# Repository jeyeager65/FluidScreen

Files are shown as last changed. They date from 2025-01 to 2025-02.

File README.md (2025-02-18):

# FluidScreen
Wireless controller for FluidNC

e19302e4588211ce1077c6e39101f643c2d2b93d


## Overview
This is a wireless controller (except for power) for a 3 axis CNC machine running FluidNC.  It connects to FluidNC via a WebSocket connection.  This uses an ESP32 and is written in C++ using PlatformIO.

# Features
- General - Hold, Resume, Unlock, Reset
- Jogging - In XY, X, Y, or Z using the physical joystick.  The further the joystick is from the center, the faster the feedrate.  The value does have a curve to make it easier to perform slow jogging with small movements.
- Home - All, X, Y, or Z
- Macro - Special macro format using GCode parameters and expression functionality of FluidNC.  Supports up to 6 custom defined macros with a description of each displayed on the screen.
- Configuration - Display a captive portal webpage for updating configuration.
  - Wifi/FluidNC - Set Wifi and FluidNC settings.
  - Theming - This is a bit extra but the individual theme and status colors can be updated.
- Hold Messages - Displays the last message on the screen.  When a hold occurs, the last message is displayed with the Resume option activated.

# Parts

## Hardware
> The 3D printed case was made for these specific components. If alternates are used, I am not certain if things will fit properly.
- 1x ESP32 Devkit - https://www.amazon.com/Espressif-ESP32-DevKitC-32E-Development-Board/dp/B09MQJWQN2
- 1x Joystick - https://www.amazon.com/gp/product/B0CPFDKWZF
- 1x Rotary Encoder - https://www.amazon.com/gp/product/B06XQTHDRR
- 1x Display - https://www.amazon.com/gp/product/B073R7BH1B
- 1x 10uF Capacitor - This allows for flashing the firmware without needing to press the Boot button on the ESP32. Otherwise, the ESP32 would need to be removed to access the Boot button.

## Miscellaneous
- ~16x M3x6mm Screws
- Female to Female Dupont Wires
- Dupont Connector Kit - This is optional. It is helpful to have a 9 or 10 plug connector for combining all the wires for the screen into a single plug. https://www.amazon.com/gp/product/B08X6C7PZM
- USB Micro Cable - For power and flashing firmware.  Ensure it is a data and power cable, not just power only.
- Solder Seal Heat Shrink Butt Connectors - This is optional and was used for joining wires to share 3.3v and ground. Used the red 18-22 awg from this kit: https://www.amazon.com/dp/B083LZS69N
  - Heat Gun - https://www.amazon.com/dp/B08VFY8THD

## 3D Print
> These were printed in PLA with 3 walls and 50% infill with a 0.4mm nozzle at 0.2mm layer height.
- 1x Case Top - Print with flat part on build plate. No supports necessary.
- 1x Case Bottom - Print with flat part on build plate. Supports required for screw holes on bottom.
- 1x ESP32 Holder - Print with flat part on build plate.  Supports required for screw holes on bottom.
- 1x Encoder Knob - Print with flat part on build plate.  Supports may be required for indent.
- 4x Washer - This is optional. A few M3 washers can be used instead. This is necessary for attaching the screen to the case top because otherwise the M3x6mm screws are too long.  Alternatively, M3x4mm screws could be used.

# Firmware

## Pre-Requisites
1. Visual Studio Code (https://code.visualstudio.com/) with "PlatformIO IDE" extension installed.
2. Silicon Labs CP210x USB to UART Bridge Driver (https://www.silabs.com/developer-tools/usb-to-uart-bridge-vcp-drivers?tab=downloads)
3. Download or checkout this repository.

## Installation
> Note: If this project has not been assembled yet or the ESP32 is standalone, the "Boot" button on the ESP32 will need to be held for a couple seconds when it starts to upload the filesystem image and when it flashes the firmware.

1. Open the Source folder in Visual Studio Code.
2. Connect the ESP32 to the computer with a USB cable.
3. Click the PlatformIO icon on the left.
4. Under "Project Tasks", select "esp32dev" -> "Platform", select the "Build Filesystem Image" task to create the filesystem image.
5. Under "Platform", select the "Upload Filesystem Image" task to upload.
6. Under "Project Tasks", select "esp32dev" -> "General", select the "Build" task to build the project.
7. Under "General", select the "Upload" task to upload the firmware.

# Assembly







## Pin Mappings

### Display
> Note: Touch Pins are not used.

| Pin | ESP32 Pin |
| --- | --- |
| VCC | 3V3 |
| GND | GND |
| CS | 5 |
| RESET | 17 |
| DC | 16 |
| SDI(MOSI) | 23 |
| SCK | 18 |
| LED | 22 |
| SDI(MISO) | 19 |

### Joystick
> Note: SW pin is not used.

| Pin | ESP32 Pin |
| --- | --- |
| GND | GND |
| +5V | 3V3 |
| VRX | 32 |
| VRY | 33 |

### Rotary Encoder
| Pin | ESP32 Pin |
| --- | --- |
| GND | GND |
| + | 3V3 |
| SW  | 27 |
| DT  | 25 |
| CLK | 26 |

### Capacitor
| Pin | ESP32 Pin |
| --- | --- |
| Short Leg with White | GND |
| Long Leg | EN |

## Steps
> With the pin mappings and pictures, it can likely be assembled without these instructions.

### Bottom
1. Start with the case bottom (thinner part with USB hole at the bottom).
2. Attach the joystick and rotary encoder with M3x6mm screws with male pins pointed at the bottom.
3. Place the ESP32 upside down with the antenna at the top. It should rest on the standoffs.
4. Attach the ESP32 holder with M3x6mm screws with the flat part up.  It should bend to apply some pressure to the ESP32 to hold it in place.
5. Create wire for sharing 3.3v connection with 4 ends, 2 on each side.  Verify lengths are appropriate and ensure there is extra length for removal of the top.  This can be done with solder seal heat shrink butt connectors, lever nuts, or just solder and heat shrink.
6. Run the wire under the bottom part of the ESP32 close to the USB end.
7. Connect the 3.3V wires to the appropriate pins on the ESP32, joystick, rotary encoder, and display.
8. Create wire for sharing GND connection with 3 ends.  This is for connecting the joystick and display. (The ESP32 has 3 GND connections. The capacitor and rotary encoder can use their own pins.)
9. Connect the GND wires to the appropriate pins on the ESP32 and joystick.
10. Connect a separate ground wire between the ESP32 and rotary encoder.
11. Connect the remaining wires for the joystick and rotary encoder as described in the pin mapping section.
12. Crimp connectors to the 10uF capacitor and attach to the ESP32 between the EN and GND pins towards the top of the connector. Ensure the short leg with the white line attaches to the GND pin.

### Top
1. Place the screen into the case top with the pins on the joystick side. The screen should be about 1mm below the surface.
2. Attach the screen with M3x6mm screws and printed washers (or 4mm screws or ~3 M3 washers).
3. Connect the wires for the display.  It is recommended to use a 9 or 10 pin dupont connector to create a single connection to the display.  This can be done making your own cables or by removing the single plastic housing and plugging it into the new larger connector.

### Finish
1. Attach the case bottom to the case top with 4 M3x6mm screws. These screws can be longer.
2. Press the printed knob onto the rotary encoder.

# Macros
The macro menu allows for up to 6 custom defined macros.  These are defined in a file that must be named "_screenmacros.gcode" and placed in the root on the SD card.

## Template
``` gcode
o100 if[#<_screenMacro> EQ 1]
  o101 if[#<_screenMacroInfoOnly> EQ 1]
    (MSG, Macro 1 - Description)
  o101 else
    (MSG, Running Macro 1)
  o101 end if
o100 elseif[#<_screenMacro> EQ 2]
  o102 if[#<_screenMacroInfoOnly> EQ 1]
    (MSG, Macro 2 - Description)
  o102 else
    (MSG, Running Macro 2)
  o102 end if
o100 elseif[#<_screenMacro> EQ 2]
  o103 if[#<_screenMacroInfoOnly> EQ 1]
    (MSG, Macro 3 - Description)
  o103 else
    (MSG, Running Macro 3)
  o103 end if
o100 elseif[#<_screenMacro> EQ 4]
  o104 if[#<_screenMacroInfoOnly> EQ 1]
    (MSG, Macro 4 - Description)
  o104 else
    (MSG, Running Macro 4)
  o104 end if
o100 elseif[#<_screenMacro> EQ 5]
  o105 if[#<_screenMacroInfoOnly> EQ 1]
    (MSG, Macro 5 - Description)
  o105 else
    (MSG, Running Macro 5)
  o105 end if
o100 elseif[#<_screenMacro> EQ 6]
  o106 if[#<_screenMacroInfoOnly> EQ 1]
    (MSG, Macro 6 - Description)
  o106 else
    (MSG, Running Macro 6)
  o106 end if
o100 else
  (PRINT, Macro %d#<_screenMacro>: Not Defined)
o100 end if
```

## How It Works
This utilizes the GCode Parameters and Expressions functionality in FluidNC: http://wiki.fluidnc.com/en/features/gcode_parameters_expressions

When highlighting a macro number on the screen, the following code is run to set the variables where "N" is the highlighted macro number:
``` gcode
#<_screenMacroInfoOnly>=1
#<_screenMacro>=N
$SD/Run=_screenmacros.gcode
```

## Example
``` gcode
o100 if[#<_screenMacro> EQ 1]
  o101 if[#<_screenMacroInfoOnly> EQ 1]
    (MSG, Run Current GCode - Run the GCode file defined in /ScreenMacros/current.gcode.)
  o101 else
    (MSG, Running Current GCode Macro)
    $SD/Run=/ScreenMacros/current.gcode
  o101 end if
o100 elseif[#<_screenMacro> EQ 2]
  o102 if[#<_screenMacroInfoOnly> EQ 1]
    (MSG, View Pulloffs - View the current X, Y, and Z pulloffs.)
  o102 else
    (MSG, Running View Pulloffs Macro)
    M0 (PRINT, Motor Pulloffs: X=%.3f#</axes/x/motor0/pulloff_mm>  Y0=%.3f#</axes/y/motor0/pulloff_mm>  Y1=%.3f#</axes/y/motor1/pulloff_mm>  Z0=%.3f#</axes/z/motor0/pulloff_mm>  Z1=%.3f#</axes/z/motor1/pulloff_mm>)
  o102 end if
o100 elseif[#<_screenMacro> EQ 3]
  o103 if[#<_screenMacroInfoOnly> EQ 1]
    (MSG, Z Level - Z level the gantry by probing Z on both sides and setting set Z pulloffs.)
  o103 else
    (MSG, Running Z Level Macro)
    $SD/Run=_zlevel.gcode
  o103 end if
o100 else
  (PRINT, Macro %d#<_screenMacro>: Not Defined)
o100 end if
```

When clicking on the highlighted macro, the same code is run except the _screenMacroInfoOnly variable is set to 0 (false).

This allows the script to know which macro and whether or not it should just display a description message or actually run the macro.

# Notes

## Future Enhancements
> None of these are guaranteed but are things I would like to do in the future.
- Add battery with charging circuit
- Add a dock (or even a magnetic charging dock)
- Make the case thinner possibly by using a mini ESP32 instead of a devkit

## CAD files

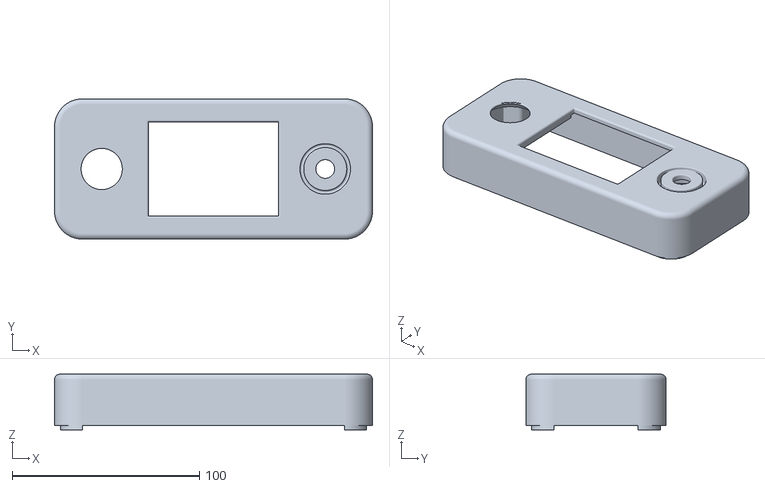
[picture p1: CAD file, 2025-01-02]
3dPrint/Case Top.stl
170.0 x 75.0 x 29.8

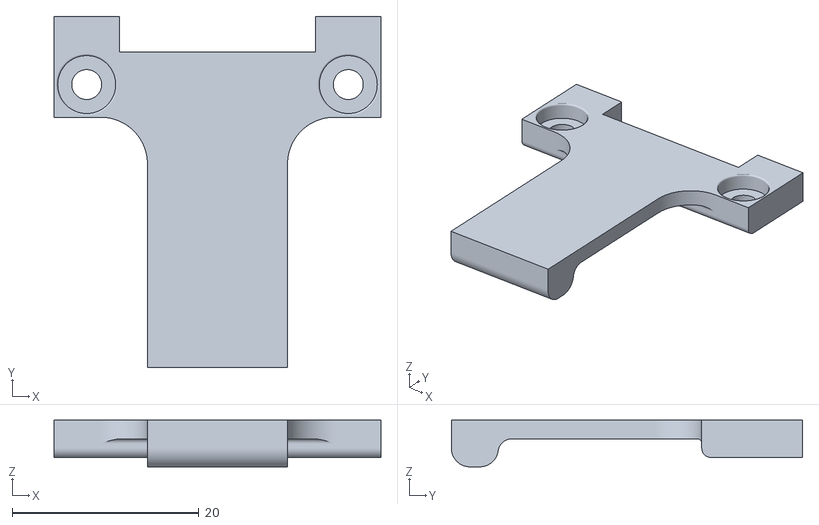
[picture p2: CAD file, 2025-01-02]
3dPrint/ESP32 Holder.stl
35.0 x 37.6 x 5.00

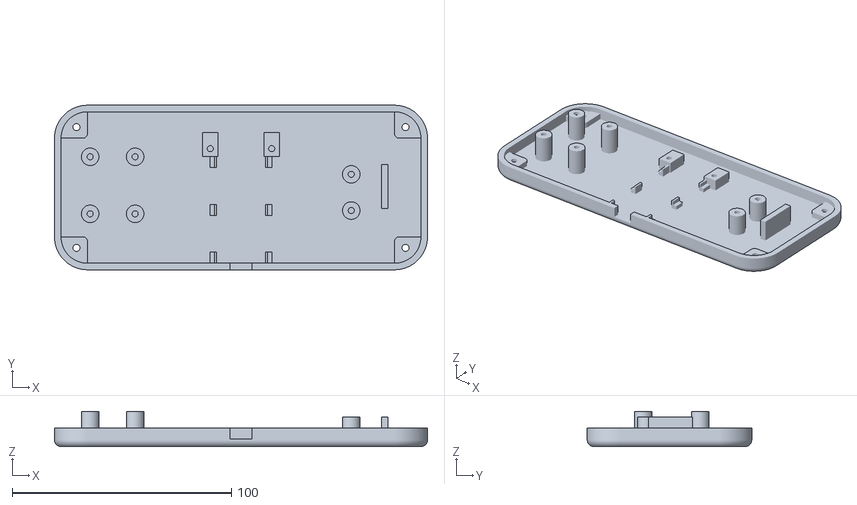
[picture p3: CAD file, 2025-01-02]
3dPrint/Case Bottom.stl
170.0 x 75.0 x 16.0

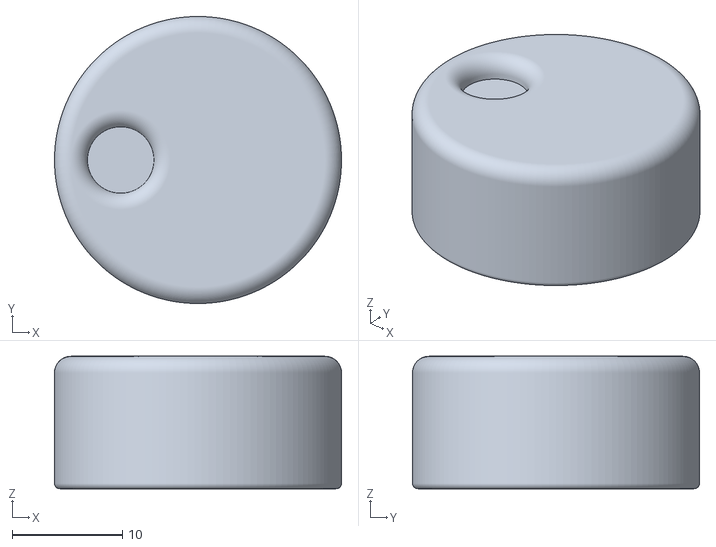
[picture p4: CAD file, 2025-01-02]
3dPrint/Knob.stl
26.0 x 26.0 x 12.0

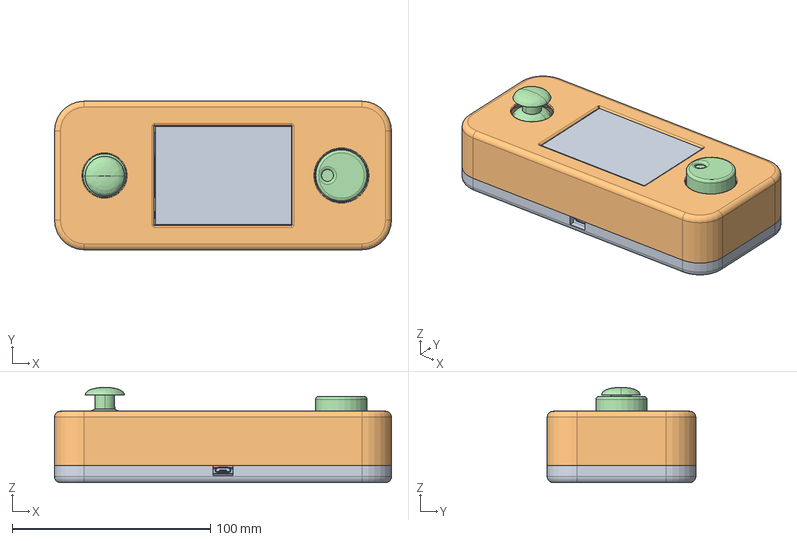
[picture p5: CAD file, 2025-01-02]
3dPrint/FluidScreen.FCStd
170.0 x 75.0 x 48.0 mm
Case Bottom
Case Top
ESP32 Holder
Knob
plate and holes
circle001
circle002
circle003
circle004
border001
border002
ShapeString099
ShapeString100
ShapeString102
ShapeString103
cupper_upper
cupper_bottom
mask_bottom
res_silk
res_silk001
res_silk002
res_silk003
res_silk004
res_silk005
cap_silk_up
cap_silk_dwn
cap_silk_up001
cap_silk_dwn001
sot23_left
sot23_right
sot23_left001
sot23_right001
u2_silk002
sd_silk001
line_silk001
line_silk002
ShapeString067
ShapeString105
ShapeString106
ShapeString107
ShapeString108
ShapeString068
ShapeString110
ShapeString111
ShapeString112
ShapeString113
ShapeString069
ShapeString115
ShapeString116
ShapeString117
ShapeString070
ShapeString119
ShapeString120
ShapeString121
ShapeString122
ShapeString071
ShapeString124
ShapeString125
ShapeString126
ShapeString073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

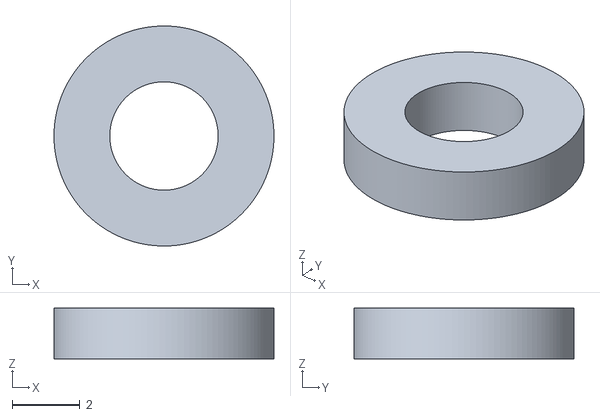
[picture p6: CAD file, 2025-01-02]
3dPrint/Washer.stl
6.50 x 6.50 x 1.50

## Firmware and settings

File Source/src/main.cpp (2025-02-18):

#include <Adafruit_GFX.h>
#include <Adafruit_ILI9341.h>
#include <Fonts/FreeSans9pt7b.h>
#include <Fonts/FreeSansBold12pt7b.h>
#include <Fonts/FreeSans12pt7b.h>
#include <Fonts/FreeMono9pt7b.h>
#include <Arduino.h>
#include <math.h>
#include <WiFi.h>
#include <WebSocketsClient.h>
#include "JogJoystick.h"
#include <ESPRotary.h>
#include "menu.h"
#include "qrcode.h"
#include "FluidScreenSettings.h"

void setupColors(FluidScreenSettings& settings);
void drawConfig();
void drawPreview();
void drawMessage();
void drawMessage(String message);
void initWebSocket();

#include "CaptivePortal.h"
#include "SPIFFS.h"

const char* version = "1.0.1-20250218";

bool wsFirstConnectAttempt = true;
bool wsDisconnected = false;

// Rotary Encoder Settings
volatile int encoderCounter = 0;
int encoderPrevCounter;
volatile int encoderMaxCount = 20;
int buttonState;
unsigned long lastButtonTime = 0;

const byte ENCODER_CLK_PIN = 25;
const byte ENCODER_DT_PIN = 26;
const byte ENCODER_SW_PIN = 27;

const int tftWidth = 320;
const int tftHeight = 240;

// Info Screen
String messageCurrent;
String messagePrevious;


ESPRotary menuEncoder;
hw_timer_t *timer = NULL;

void IRAM_ATTR handleLoop() {
  menuEncoder.loop();
}

// Joystick Canvas
GFXcanvas16 joystickCanvas(120, 120);
GFXcanvas16 jsInfoCanvas(100, 100);

// Joystick Pins
const int JOYSTICK_X_PIN = 33;
const int JOYSTICK_Y_PIN = 32;

// Display TFT Pins
const int TFT_CS_PIN = 5;
const int TFT_DC_PIN = 16;
const int TFT_RST_PIN = 17;
const int TFT_BL_PIN = 22;

unsigned long lastDrawTime = 0;
unsigned long drawDelay = 50;

unsigned long lastMacroInfoTime = 0;
unsigned long macroInfoDelay = 300;

uint16_t feedrate = 0;
unsigned long lastJogTime = 0;
unsigned long jogDelay = 200;
bool jogActive = false;

// Colors
// RGB565 Colors - https://learn.adafruit.com/adafruit-gfx-graphics-library/coordinate-system-and-units
// Converter - https://barth-dev.de/online/rgb565-color-picker/
uint16_t COLOR_PRIMARY           = 0x01EC;  // #003d63
uint16_t COLOR_SECONDARY         = 0x434F;  // #42697b
uint16_t COLOR_BG                = 0x0841;  // #080808
uint16_t COLOR_BG_ALT            = 0x39C7;  // #3a393a
uint16_t COLOR_BG_PANEL          = 0x2104;  // #212021
uint16_t COLOR_BORDER            = 0xBE19;  // #bdc2ce
uint16_t COLOR_SELECT            = 0x0397;  // #0071bd
uint16_t COLOR_TEXT              = 0xFFFF;  // #ffffff
uint16_t COLOR_QR                = 0x0000;  // #000000
uint16_t COLOR_QR_BG             = 0xFFFF;  // #ffffff

uint16_t COLOR_STATUS_DEFAULT    = 0x7BEF;  // #7b7d7b
uint16_t COLOR_STATUS_IDLE       = 0x7BEF;  // #7b7d7b
uint16_t COLOR_STATUS_JOG        = 0x000F;  // #00007b
uint16_t COLOR_STATUS_RUN        = 0x03E0;  // #007d00
uint16_t COLOR_STATUS_HOLD       = 0xE660;  // #e6ce00
uint16_t COLOR_STATUS_HOME       = 0x03EF;  // #007d7b
uint16_t COLOR_STATUS_ALARM      = 0xF800;  // #ff0000
uint16_t COLOR_STATUS_DISCONNECT = 0x780F;  // #7b007b
uint16_t COLOR_STATUS_CONFIG     = 0xFB80;  // #ff7100

uint16_t JOG_MAX_FEEDRATE_XY     = 2400;
uint16_t JOG_MAX_FEEDRATE_Z      = 800;

// Display Values
String grblState = "UNKNOWN";
String grblStatePrev = "UNKNOWN";
String mPosX = " ", mPosY = " ", mPosZ = " ";
String mPosXPrev = "*", mPosYPrev = "*", mPosZPrev = "*";
String lastMessage;

JogJoystick joystick(JOYSTICK_X_PIN, JOYSTICK_Y_PIN);

Adafruit_ILI9341 tft = Adafruit_ILI9341(TFT_CS_PIN, TFT_DC_PIN, TFT_RST_PIN);

WebSocketsClient webSocket;

bool initWiFi() 
{
  if(WiFi.status() == WL_CONNECTED) {
    return true;
  }

  int retryCount = 20;
  WiFi.mode(WIFI_STA);
  WiFi.setAutoReconnect(true);
  WiFi.begin(CurrentSettings.Connection.SSID, CurrentSettings.Connection.Password);
  Serial.print("Connecting to WiFi ..");
  while (WiFi.status() != WL_CONNECTED) {
    Serial.print('.');

    if(retryCount > 0) {
      delay(1000);
      retryCount--;
    }
    else {
      WiFi.setAutoReconnect(false);
      return false;
    }
  }
  Serial.println(WiFi.localIP());
  return true;
}

String convert(uint8_t *str, int length)
{
  return String((char *)str, length);
}

void setupTextArea(int x, int y, int width, int height, bool drawBorder = false, int leftMargin = 0, int lineHeight = 30, int negYOffset = 10, uint16_t bgColor = COLOR_BG) {
  tft.setCursor(x+leftMargin, y+lineHeight-negYOffset);
  tft.fillRect(x, y, width, height, bgColor);
  
  if(drawBorder) {
    tft.drawRect(x, y, width, height, COLOR_BORDER);
  }
  
  tft.setTextColor(COLOR_TEXT);
  tft.setFont(&FreeSans9pt7b);
}

void drawSubMenu(const String* subMenu, const int subMenuSize, int subMenuSelected) {
  int menuHeight = 24;

  tft.fillRect(0, 240-(menuHeight*2), 320, menuHeight, COLOR_SECONDARY);
  tft.drawRect(0, 240-(menuHeight*2), 320, menuHeight, COLOR_BORDER);

  int itemSize = 320/subMenuSize;
  int rightX = 0;
  for(int j = 0; j < subMenuSize; j++) {
    tft.setCursor(j*itemSize, 234-menuHeight);
    tft.setFont(&FreeSans9pt7b);
    if(j == subMenuSelected) {
      tft.fillRect((j*itemSize)+1,240-(menuHeight*2)+1,itemSize-1,menuHeight-2,COLOR_SELECT);
    }
    tft.setTextColor(COLOR_TEXT);

    int16_t x1, y1, xCenterStart;
    uint16_t width, height;
    tft.getTextBounds(subMenu[j], j*itemSize, 234-menuHeight, &x1, &y1, &width, &height);
    xCenterStart = x1 + (width/2);

    tft.setCursor((j*itemSize) + ((itemSize-width)/2), 234-menuHeight);
    tft.print(subMenu[j]);
    tft.drawLine((j+1)*itemSize, 240-(menuHeight*2), (j+1)*itemSize, 240-menuHeight, COLOR_BORDER);
  }
}

void drawMenu() {
  int menuHeight = 24;

  tft.fillRect(0, 240-menuHeight, 320, menuHeight, COLOR_PRIMARY);
  tft.drawRect(0, 240-menuHeight, 320, menuHeight, COLOR_BORDER);

  int itemSize = 320/menuSize;
  
  for(int i = 0; i < menuSize; i++) {
    tft.setCursor(i*itemSize, 234);
    tft.setFont(&FreeSans9pt7b);
    if(i == menuSelected) {
      tft.fillRect((i*itemSize)+1,240-menuHeight+1,itemSize-1,menuHeight-2,COLOR_SELECT);
    }
    tft.setTextColor(COLOR_TEXT);

    // Center Text
    int16_t x1, y1, xCenterStart;
    uint16_t width, height;
    tft.getTextBounds(menu[i], i*itemSize, 234, &x1, &y1, &width, &height);
    xCenterStart = x1 + (width/2);

    tft.setCursor(x1 + ((itemSize-width)/2), 234);
    tft.print(menu[i]);
    tft.drawLine((i+1)*itemSize, 240-menuHeight, (i+1)*itemSize, 240, COLOR_BORDER);
  }

  // Draw submenu
  tft.fillRect(0, 240-(menuHeight*2), 320, menuHeight, COLOR_PRIMARY);
  tft.drawRect(0, 240-(menuHeight*2), 320, menuHeight, COLOR_BORDER);

  if(menu[menuSelected] == "Jog") {
    drawSubMenu(jogMenu, jogMenuSize, jogMenuSelected);
  }
  else if(menu[menuSelected] == "Home") {
    drawSubMenu(homeMenu, homeMenuSize, homeMenuSelected);
  }
  else if(menu[menuSelected] == "Macro") {
    drawSubMenu(macroMenu, macroMenuSize, macroMenuSelected);

    // Ensure macro message is displayed
    if(macroMenuSelected == 0) {
      drawMessage(macroMessage);
    }
  }
  else if(menu[menuSelected] == "Other") {
    drawSubMenu(otherMenu, otherMenuSize, otherMenuSelected);
  }
  else if(menu[menuSelected] == "Main") {
    drawSubMenu(controlMenu, controlMenuSize, controlMenuSelected);
  }
}

void drawMessage(String message) {
  int16_t x1, y1;
  uint16_t width, height;

  setupTextArea(0,50,320,135);

  tft.fillRoundRect(0,50+5, 320, 135-5, 5, COLOR_BG_ALT);
  tft.drawRoundRect(0,50+5, 320, 135-5, 5, COLOR_BORDER);

  // Clean Message
  if(message.startsWith("[MSG:")) {
    int startIndex = message.indexOf(":", 5)+2;
    int tempStartIndex = message.indexOf(",", startIndex+1);
    if(tempStartIndex >= 0) { startIndex = tempStartIndex+2; }
    int endIndex = message.lastIndexOf("]");
    message = message.substring(startIndex, endIndex);
  }

  message.trim();

  // Break at spaces
  bool includeSpace = false;
  char * ptr;
  int length = message.length();
  char buffer[length];
  sprintf(buffer, "%s", message.c_str());

  tft.setFont(&FreeSans9pt7b);
  
  tft.setCursor(5,74);
  tft.setTextWrap(true);

  ptr = strtok(buffer, " ");
  while (ptr != NULL)
  {
    tft.getTextBounds(ptr, tft.getCursorX(), tft.getCursorY(), &x1, &y1, &width, &height);

    if(x1 + width > 320-20) {
      tft.println("");
      tft.setCursor(5, tft.getCursorY());
      includeSpace = false;
    }

    if(includeSpace) {
      tft.print(" ");
    }
    
    tft.printf("%s", ptr);
    ptr = strtok(NULL, " ");
    includeSpace = true;
  }
}

void drawMessage() {
  drawMessage(lastMessage); 
}

void drawStatus(String status, bool preventDuplicate = true) {
  bool isHold = status.startsWith("Hold");
  bool isAlarm = status == "Alarm";
  
  grblState = status;
  if(preventDuplicate && grblState == grblStatePrev) return;

  grblStatePrev = grblState;

  tft.setCursor(0, 0+30-7);
  tft.setTextColor(COLOR_TEXT);

  uint16_t statusColor = COLOR_STATUS_DEFAULT;
  if(status == "Idle") statusColor = COLOR_STATUS_IDLE;
  else if(status == "Jog") statusColor = COLOR_STATUS_JOG;
  else if(status == "Run") statusColor = COLOR_STATUS_RUN;
  else if(status.startsWith("Hold")) statusColor = COLOR_STATUS_HOLD;
  else if(status == "Home") statusColor = COLOR_STATUS_HOME;
  else if(status == "Alarm") statusColor = COLOR_STATUS_ALARM;
  else if(status == "Disconnected") statusColor = COLOR_STATUS_DISCONNECT;
  else if(status == "Configuration") statusColor = COLOR_STATUS_CONFIG;

  tft.fillRect(0, 0, 320, 30, statusColor);
  tft.drawRect(0, 0, 320, 30, COLOR_BORDER);

  // Override Font
  tft.setFont(&FreeSansBold12pt7b);
  
  status.toUpperCase();

  int16_t x1, y1, xCenterStart;
  uint16_t width, height;
  tft.getTextBounds(status, 0, 0, &x1, &y1, &width, &height);
  xCenterStart = x1 + (width/2);
  tft.setCursor(x1 + ((320-width)/2), 0+30-7);

  tft.printf("%s", status);

  // Auto-select Resume when Hold occurs
  if(isHold) {
    menuSelected = 0; // Main
    controlMenuSelected = 2; // Resume
    menuLevel = 1;
    encoderMaxCount = controlMenuSize-1;
    encoderPrevCounter = -1;
    encoderCounter = controlMenuSelected;
    menuEncoder.setUpperBound(encoderMaxCount);
    menuEncoder.resetPosition(encoderCounter);
  } else if(isAlarm) {
    // Auto-select Reset when Alarm occurs
    menuSelected = 0; // Main
    controlMenuSelected = 4; // Reset
    menuLevel = 1;
    encoderMaxCount = controlMenuSize-1;
    encoderPrevCounter = -1;
    encoderCounter = controlMenuSelected;
    menuEncoder.setUpperBound(encoderMaxCount);
    menuEncoder.resetPosition(encoderCounter);
  }
}

void drawPosition(String mPosX, String mPosY, String mPosZ) {
  if(mPosX != mPosXPrev) 
  { 
    setupTextArea(0,30-1,320/3,20, true, 2, 20, 5, COLOR_BG_PANEL); 
    tft.printf("X: %s", mPosX); 
  }
  
  if(mPosY != mPosYPrev)
  { 
    setupTextArea(0+(320/3)*1,30-1,320/3,20, true, 2, 20, 5, COLOR_BG_PANEL);
    tft.printf("Y: %s", mPosY); 
  }
  
  if(mPosZ != mPosZPrev)
  { 
    setupTextArea(0+(320/3)*2,30-1,320-((320/3)*2),20, true, 2, 20, 5, COLOR_BG_PANEL);
    tft.printf("Z: %s", mPosZ); 
  }

  mPosXPrev = mPosX;
  mPosYPrev = mPosY;
  mPosZPrev = mPosZ;
}
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
void loop() {
  if(CurrentSettings.IsConfigMode) {
    captivePortalLoop();
    return;
  }

  if(!wsDisconnected) { webSocket.loop(); }

  // Process joystick if Jog menu active
  if(menu[menuSelected] == "Jog" && menuLevel == 1) {
    joystick.loop();
  }

  // Process button presses
  int buttonStateCurr = digitalRead(ENCODER_SW_PIN);
  if((millis() - lastButtonTime) > 100) {
    if(buttonStateCurr != buttonState) {
      buttonState = buttonStateCurr;

      if(buttonState == LOW) {
        handleButtonPress();
      }
      lastButtonTime = millis();
    }
  }

  // Redraw Menu if Encoder Changed
  if (encoderPrevCounter != encoderCounter) {
    encoderPrevCounter = encoderCounter;

    if (menu[menuSelected] == "Jog" && menuLevel == 1) {
      setupTextArea(0, 50, 320, 135);
    }
    else if (menu[menuSelected] == "Macro" && menuLevel == 1 && macroMenuSelected > 0) {
      // Debounce getting macro info
      if ((millis() - lastMacroInfoTime) > macroInfoDelay) {
        // Set to only display macro info
        webSocket.sendTXT("#<_screenMacroInfoOnly>=1\n");

        // Set specific macro number to get info for
        String command = "#<_screenMacro>=" + macroMenu[macroMenuSelected] + "\n";

        webSocket.sendTXT(command);
        webSocket.sendTXT("$SD/Run=_screenmacros.gcode\n");
        lastMacroInfoTime = millis();
      } else {
        encoderPrevCounter = -1; // Reset counter so it gets rechecked
        drawMessage("Loading...");
      }
    }
    else if(menu[menuSelected] == "Other" && menuLevel == 1) {
      if(otherMenu[otherMenuSelected] == "Conn") {
        drawMessage(otherConnMessage);
      } else if(otherMenu[otherMenuSelected] == "Setup") {
        drawMessage(otherSetupMessage);
      } else if(otherMenu[otherMenuSelected] == "Info") {
        drawMessage(otherInfoMessage);
      }
    }

    // Reset Message when returning to Back submenu item
    if(menuLevel == 1) {
      if(menu[menuSelected] == "Jog" && jogMenuSelected == 0) {
        drawMessage(jogMessage);
      }
      //else if(menu[menuSelected] == "Home" && homeMenuSelected == 0) {
      //  drawMessage(homeMessage);
      //}
      else if(menu[menuSelected] == "Macro" && macroMenuSelected == 0) {
        drawMessage(macroMessage);
      }
      else if(menu[menuSelected] == "Other" && otherMenuSelected == 0) {
        drawMessage(otherMessage);
      }
      //else if(menu[menuSelected] == "Main" && controlMenuSelected == 0) {
      //  drawMessage(controlMenuMessage);
      //}
    }

    drawMenu();
  }

  if(menu[menuSelected] == "Jog" && menuLevel == 1) 
  {
    Position position = joystick.getPosition();
    
    if(millis() - lastDrawTime > drawDelay) {
      // Feedrate - base on max axis
      if(jogMenu[jogMenuSelected] == "XY") {
        feedrate = JOG_MAX_FEEDRATE_XY * ((float)abs(position.x)/100);
        if(abs(position.x) < abs(position.y)) {
          feedrate = JOG_MAX_FEEDRATE_XY * ((float)abs(position.y)/100);
        }

        jsInfoCanvas.fillScreen(COLOR_BG);
        jsInfoCanvas.setFont(&FreeSans9pt7b);
        jsInfoCanvas.setTextColor(COLOR_TEXT);
        jsInfoCanvas.setCursor(0, 12);
        jsInfoCanvas.printf("X: %i%%\n", position.x);
        jsInfoCanvas.printf("Y: %i%%\n", position.y*-1); // Invert Y sign
        jsInfoCanvas.printf("F: %i\n", feedrate);
        tft.drawRGBBitmap(0, 60, jsInfoCanvas.getBuffer(), jsInfoCanvas.width(), jsInfoCanvas.height());

        joystickCanvas.fillScreen(COLOR_BG);
        joystickCanvas.fillRoundRect(0, 0, 120, 120, 5, COLOR_BG_PANEL);
        joystickCanvas.drawRoundRect(0, 0, 120, 120, 5, COLOR_BORDER);
        joystickCanvas.fillCircle(120/2, 120/2, 45, COLOR_BG_ALT);
        joystickCanvas.drawCircle(120/2, 120/2, 45, COLOR_BORDER);
        joystickCanvas.drawLine(120/2, 0, 120/2, 120, COLOR_BORDER);
        joystickCanvas.drawLine(0, 120/2, 120, 120/2, COLOR_BORDER);
        joystickCanvas.setFont();
        joystickCanvas.setTextColor(COLOR_TEXT);
        joystickCanvas.setCursor((120/2)+2, 5);
        joystickCanvas.print("Y+");
        joystickCanvas.setCursor((120/2)+2, 120-11);
        joystickCanvas.print("Y-");
        joystickCanvas.setCursor(2, (120/2)-8);
        joystickCanvas.print("X-");
        joystickCanvas.setCursor(120-12, (120/2)-8);
        joystickCanvas.print("X+");

        int centerX = 120/2;
        int centerY = 120/2;
        int joyPosX = centerX + (position.x*((float)45/100));
        int joyPosY = centerY + (position.y*((float)45/100));

        joystickCanvas.fillCircle(joyPosX, joyPosY, 10, COLOR_SELECT);
        joystickCanvas.drawCircle(joyPosX, joyPosY, 10, COLOR_BORDER);
        joystickCanvas.fillCircle(joyPosX, joyPosY, 2, COLOR_BORDER);

        tft.drawRGBBitmap((320/2)-(joystickCanvas.width()/2), 60, joystickCanvas.getBuffer(), joystickCanvas.width(), joystickCanvas.height());
      }
      else if(jogMenu[jogMenuSelected] == "X") {
        feedrate = JOG_MAX_FEEDRATE_XY * ((float)abs(position.x)/100);

        jsInfoCanvas.fillScreen(COLOR_BG);
        jsInfoCanvas.setFont(&FreeSans9pt7b);
        jsInfoCanvas.setTextColor(COLOR_TEXT);
        jsInfoCanvas.setCursor(0, 12);
        jsInfoCanvas.printf("X: %i%%\n", position.x);
        jsInfoCanvas.printf("F: %i\n", feedrate);
        tft.drawRGBBitmap(0, 60, jsInfoCanvas.getBuffer(), jsInfoCanvas.width(), jsInfoCanvas.height());
        
        joystickCanvas.fillScreen(COLOR_BG);
        joystickCanvas.fillRoundRect(0, 0, 120, 120, 5, COLOR_BG_PANEL);
        joystickCanvas.drawRoundRect(0, 0, 120, 120, 5, COLOR_BORDER);

        joystickCanvas.fillCircle(27, 120/2, 12, COLOR_BG_ALT);
        joystickCanvas.drawCircle(27, 120/2, 12, COLOR_BORDER);
        joystickCanvas.fillCircle(120-27, 120/2, 12, COLOR_BG_ALT);
        joystickCanvas.drawCircle(120-27, 120/2, 12, COLOR_BORDER);
        joystickCanvas.fillRect(27, (120/2)-12, 120-(27*2), 12*2, COLOR_BG_ALT);
        joystickCanvas.drawLine(27, (120/2)-12, 120-27, (120/2)-12, COLOR_BORDER);
        joystickCanvas.drawLine(27, (120/2)+12, 120-27, (120/2)+12, COLOR_BORDER);
        
        joystickCanvas.drawLine(120/2, 40, 120/2, 80, COLOR_BORDER);
        joystickCanvas.drawLine(0, 120/2, 120, 120/2, COLOR_BORDER);
        joystickCanvas.setFont();
        joystickCanvas.setTextColor(COLOR_TEXT);
        joystickCanvas.setCursor(2, (120/2)-8);
        joystickCanvas.print("X-");
        joystickCanvas.setCursor(120-12, (120/2)-8);
        joystickCanvas.print("X+");

        int centerX = 120/2;
        int centerY = 120/2;
        int joyPosX = centerX + (position.x*((float)45/100));
        int joyPosY = centerY;

        joystickCanvas.fillCircle(joyPosX, joyPosY, 10, COLOR_SELECT);
        joystickCanvas.drawCircle(joyPosX, joyPosY, 10, COLOR_BORDER);
        joystickCanvas.fillCircle(joyPosX, joyPosY, 2, COLOR_BORDER);

        tft.drawRGBBitmap((320/2)-(joystickCanvas.width()/2), 60, joystickCanvas.getBuffer(), joystickCanvas.width(), joystickCanvas.height());
      }
      else if(jogMenu[jogMenuSelected] == "Y") {
        feedrate = JOG_MAX_FEEDRATE_XY * ((float)abs(position.y)/100);

        jsInfoCanvas.fillScreen(COLOR_BG);
        jsInfoCanvas.setFont(&FreeSans9pt7b);
        jsInfoCanvas.setTextColor(COLOR_TEXT);
        jsInfoCanvas.setCursor(0, 12);
        jsInfoCanvas.printf("Y: %i%%\n", position.y*-1); // Invert Y sign
        jsInfoCanvas.printf("F: %i\n", feedrate);
        tft.drawRGBBitmap(0, 60, jsInfoCanvas.getBuffer(), jsInfoCanvas.width(), jsInfoCanvas.height());

        joystickCanvas.fillScreen(COLOR_BG);
        joystickCanvas.fillRoundRect(0, 0, 120, 120, 5, COLOR_BG_PANEL);
        joystickCanvas.drawRoundRect(0, 0, 120, 120, 5, COLOR_BORDER);
        
        joystickCanvas.fillCircle(120/2, 27, 12, COLOR_BG_ALT);
        joystickCanvas.drawCircle(120/2, 27, 12, COLOR_BORDER);
        joystickCanvas.fillCircle(120/2, 120-27, 12, COLOR_BG_ALT);
        joystickCanvas.drawCircle(120/2, 120-27, 12, COLOR_BORDER);
        joystickCanvas.fillRect((120/2)-12, 27, 12*2, 120-(27*2), COLOR_BG_ALT);
        joystickCanvas.drawLine((120/2)-12, 27, (120/2)-12, 120-27, COLOR_BORDER);
        joystickCanvas.drawLine((120/2)+12, 27, (120/2)+12, 120-27, COLOR_BORDER);

        joystickCanvas.drawLine(120/2, 0, 120/2, 120, COLOR_BORDER);
        joystickCanvas.drawLine(40, 120/2, 80, 120/2, COLOR_BORDER);

        joystickCanvas.setFont();
        joystickCanvas.setTextColor(COLOR_TEXT);
        joystickCanvas.setCursor((120/2)+2, 5);
        joystickCanvas.print("Y+");
        joystickCanvas.setCursor((120/2)+2, 120-11);
        joystickCanvas.print("Y-");
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

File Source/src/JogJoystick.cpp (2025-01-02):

#include "JogJoystick.h"

JogJoystick::JogJoystick(byte xPin, byte yPin) 
{
    this->xPin = xPin;
    this->yPin = yPin;
    init();
}

void JogJoystick::init() 
{
    this->lastReadTime = 0;
    this->readDelay = 200;

    // Determine joystick center
    int xTemp[3], yTemp[3];
	
    for(short i=0; i<3; i++) {
        delay(100);
        xTemp[i] = analogRead(this->xPin);
        yTemp[i] = analogRead(this->yPin);
    }

    this->positionCenter.x = (int)((xTemp[0]+xTemp[1]+xTemp[2])/3);
    this->positionCenter.y = (int)((yTemp[0]+yTemp[1]+yTemp[2])/3);	
}

Position JogJoystick::getPosition()
{
    return this->position;
}

void JogJoystick::update() {
    this->positionRaw.x = analogRead(this->xPin);
    this->positionRaw.y = analogRead(this->yPin);

    int xPos, yPos, xPosMax, xPosCurr, yPosMax, yPosCurr;
    int xFix, yFix;

    if(this->positionRaw.x > this->positionCenter.x) {
        xFix = 1;
        xPosMax = 4095 - this->positionCenter.x;
        xPosCurr = this->positionRaw.x - this->positionCenter.x;
        xPos = ((float)xPosCurr/(float)xPosMax) * 1000 * xFix; // Normalize to 1000
    } else {
        xFix = -1;
        xPosMax = this->positionCenter.x;
        xPosCurr = this->positionCenter.x - this->positionRaw.x;
        xPos = ((float)xPosCurr/(float)xPosMax) * 1000 * xFix; // Normalize to 1000
    }

    if(this->positionRaw.y > this->positionCenter.y) {
        yFix = -1;
        yPosMax = 4095 - this->positionCenter.y;
        yPosCurr = this->positionRaw.y - this->positionCenter.y;
        yPos = ((float)yPosCurr/(float)yPosMax) * 1000 * yFix; // Normalize to 1000
    } else {
        yFix = 1;
        yPosMax = this->positionCenter.y;
        yPosCurr = this->positionCenter.y - this->positionRaw.y;
        yPos = ((float)yPosCurr/(float)yPosMax) * 1000 * yFix; // Normalize to 1000
    }

    // Add 2% deadzone
    if(abs(xPos) <= 20) {
        xPos = 0;
    }
    if(abs(yPos) <= 20) {
        yPos = 0;
    }

    // Add curve for more control at low end
    if(xPos != 0) {
        xPos = 0.001 * pow(xPos, 2) * xFix;
    }
    if(yPos != 0) {
        yPos = 0.001 * pow(yPos, 2) * yFix;
    }

    // Normalize to 100
    this->position.x = xPos/10;
    this->position.y = yPos/10;
}

void JogJoystick::loop() {
    if((millis() - lastReadTime) > readDelay) {
        update();
        lastReadTime = millis();
    }
}

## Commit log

2025-01-02 Initial checkin of code and 3d files
    [Case Bottom.stl, Case Top.stl, ESP32 Holder.stl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]
2025-01-31 Websocket connection fix, help messages, alarm default
    [main.cpp]
